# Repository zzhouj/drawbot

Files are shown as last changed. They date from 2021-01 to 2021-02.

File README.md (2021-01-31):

# drawbot
2040铝合金框架Core-XY结构的写字机器人

## 简介
打印机墨盒又双叕涨价了！娃经常要我帮她抄写错题，费时费力，还嫌弃我字写的难看。不如自己DIY一台写字机器人，既可以替代我抄写错题，还可以部分替代打印机的功能节省墨（Jin）盒（Qian）。

本项目主要参考了[T站](https://www.thingiverse.com/)上的[DrawBot V1.1 (Drawing Robot - Arduino Uno + CNC Shield + GRBL)](https://www.thingiverse.com/thing:2349232)。参考项目的机械部分采用了3D打印件，而我手头暂时还没有3D打印机，所以采用了2040铝合金的框架以及某宝上定制CNC切割了5块3mm铝合金板，电子部分和软件部分和参考项目一样。

做这个项目主要是考虑到DIY写字机器人相对DIY 3D打印机来说要简单很多：没有Z轴，没有热床，没有挤出机，一块Arduino Uno + CNC Shield即可控制，GRBL firmware复杂度低。我想先用写字机器人来练手，然后再来自己组装一台3D打印机。

## 目录及文件说明
- sw2020/ 存放写字机器人的零件模型及装配文件，使用的三维建模软件是SolidWorks 2020。
- dxf/ 3mm铝合金板定制CNC切割文件，由sw2020文件夹中的对应零件模型导出生成。
- bom/ 各部分材料清单。
- BOM.xls 零件清单及参考价格。
- Assemble and User Manual.pdf 装配及用户手册。

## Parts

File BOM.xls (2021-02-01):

项目号 | 零件号 | 说明 | 数量 | 单价 | 价格
1 | V-Slot 2040铝型材370mm | 欧标V-Slot | 1 | 9.22 | 9.22
2 | V-Slot 2040铝型材200mm | 欧标V-Slot | 2 | 4.98 | 9.96
3 | 7878_2020角铝20x8mm |  | 4 | 3.5 | 14
4 | T型螺母20M6 |  | 16 | 0.2 | 3.2
5 | B18.3.4M - 6 x 1.0 x 12 SBHCS --N | 圆头内六角M6*12 | 16 | 0.15 | 2.4
6 | 2040铝合金型材盖板 |  | 8 | 2.5 | 20
7 | B18.3.5M - 5 x 0.8 x 10 Socket FCHS -- 10N | 沉头内六角M5*10 | 16 | 0.21 | 3.36
8 | T型螺母20M5 |  | 16 | 0.2 | 3.2
9 | 42步进电机支架 |  | 2 | 2.9 | 5.8
10 | B18.3.4M - 4 x 0.7 x 8 SBHCS --N | 圆头内六角M4*8 | 8 | 0.06 | 0.48
11 | T型螺母20M4 |  | 8 | 0.2 | 1.6
12 | 光轴固定支架（卧式）SHF8 |  | 8 | 2.6 | 20.8
13 | 光轴8x370mm |  | 4 | 5.8 | 23.2
14 | B18.3.4M - 5 x 0.8 x 16 SBHCS --N | 圆头内六角M5*16 | 16 | 0.12 | 1.92
15 | XY轴联合支架 | 3mm铝合金板定制CNC切割 | 1 | 18 | 18
16 | 光轴轴承LM8UU |  | 8 | 2 | 16
17 | B18.3.4M - 5 x 0.8 x 25 SBHCS --N | 圆头内六角M5*25 | 4 | 0.16 | 0.64
18 | 2GT惰轮20齿无齿内孔5 带宽6mm |  | 5 | 3.1 | 15.5
19 | B18.2.4.1M - Hex nut, Style 1, M5 x 0.8 --D-N | 螺母M5 | 4 | 0.06 | 0.24
20 | B18.2.4.5M - Hex jam nut, M5 x 0.8 --D-N | 螺母M5 | 8 | 0.06 | 0.48
21 | Y轴尾端 |  | 1 | 18 | 18
22 | 圆柱销M5x25mm |  | 1 | 0.5 | 0.5
23 | Y轴首端 |  | 1 | 18 | 18
24 | 六角隔离柱M3x6mm |  | 4 | 1.56 | 6.24
25 | Y轴首端——销柱支架 |  | 1 | 18 | 18
26 | B18.3.4M - 3 x 0.5 x 6 SBHCS --N | 圆头内六角M3*6 | 6 | 0.06 | 0.36
27 | 舵机SG90 |  | 1 | 4.9 | 4.9
28 | ABS空心隔离柱5.2x11x1 2mm |  | 4 | 0.23 | 0.92
29 | 圆柱销M6x120mm |  | 2 | 0.95 | 1.9
30 | B18.2.4.5M - Hex jam nut, M5 x 0.8 --D-N | 螺母M5 | 4 | 0.06 | 0.24
31 | B18.2.4.1M - Hex nut, Style 1, M3 x 0.5 --D-N | 螺母M3 | 4 | 0.05 | 0.2
32 | Y轴首端——滑动支架 |  | 1 | 18 | 18
33 | 夹笔器 |  | 1 | 20 | 20
34 | 光轴轴承LM6UU |  | 4 | 1.4 | 5.6
35 | 42步进电机38mm | 二手拆机件 | 2 | 12.68 | 25.36
36 | 2GT同步轮20齿内孔5带 宽6mm |  | 2 | 1.7 | 3.4
37 | B18.3.1M - 3 x 0.5 x 8 Hex SHCS -- 8NHX | 杯头内六角M3*8 | 8 | 0.1 | 0.8
38 | 42步进电机硅胶减震垫片 厚2mm |  | 2 | 1.76 | 3.52
39 | Arduino Uno |  | 1 | 19.5 | 19.5
40 | CNC Shield V3 + A4988x4 |  | 1 | 19.4 | 19.4
41 | 42步进电机连接线 |  | 2 | 1.5 | 3
42 | 2GT同步带6mm |  | 2 | 2.65 | 5.3
43 | 2pin杜邦线（公对母）70cm |  | 2 | 0.8 | 1.6
44 | 六角隔离柱M3x20mm |  | 4 | 1.68 | 6.72
45 | 跳线帽 |  | 6 | 0.04 | 0.24
46 | 电源适配器12V2A |  | 1 | 12.8 | 12.8
47 | 2芯1平方保护套软电线0.2m |  | 1 | 0.26 | 0.26
48 | 电源接头DC母头 |  | 1 | 0.6 | 0.6
合计 |  |  | 225 |  | 385.36

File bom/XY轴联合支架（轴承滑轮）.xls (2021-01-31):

项目号 | 零件号 | 说明 | 数量
1 | XY轴联合支架 |  | 1
2 | 光轴轴承LM8UU |  | 8
3 | B18.3.4M - 5 x 0.8 x 25 SBHCS --N |  | 4
4 | 2GT惰轮20齿无齿内孔5 带宽6mm |  | 4
5 | B18.2.4.1M - Hex nut, Style 1, M5 x 0.8 --D-N |  | 4
6 | B18.2.4.5M - Hex jam nut, M5 x 0.8 --D-N |  | 4

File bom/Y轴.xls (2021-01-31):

项目号 | 零件号 | 说明 | 数量
1 | Y轴尾端 |  | 1
2 | 圆柱销M5x25mm |  | 1
3 | 2GT惰轮20齿无齿内孔5 带宽6mm |  | 1
4 | 光轴固定支架（卧式）SH F8 |  | 4
5 | B18.3.4M - 5 x 0.8 x 16 SBHCS --N |  | 8
6 | B18.2.4.5M - Hex jam nut, M5 x 0.8 --D-N |  | 4
7 | 光轴8x370mm |  | 2
8 | Y轴首端 |  | 1
9 | 六角隔离柱M3x6mm |  | 4
10 | Y轴首端——销柱支架 |  | 1
11 | B18.3.4M - 3 x 0.5 x 6 SBHCS --N |  | 4
12 | 舵机SG90 |  | 1
13 | ABS空心隔离柱5.2x11x1 2mm |  | 4
14 | 圆柱销M6x120mm |  | 2
15 | B18.2.4.5M - Hex jam nut, M5 x 0.8 --D-N |  | 4
16 | B18.2.4.1M - Hex nut, Style 1, M3 x 0.5 --D-N |  | 4

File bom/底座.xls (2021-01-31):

项目号 | 零件号 | 说明 | 数量
1 | V-Slot 2040铝型材370mm |  | 1
2 | V-Slot 2040铝型材200mm |  | 2
3 | 7878_2020角铝20x8m m |  | 4
4 | T型螺母20M6 |  | 16
5 | B18.3.4M - 6 x 1.0 x 12 SBHCS --N | 圆头内六角M6*12 | 16
6 | 2040铝合金型材盖板 |  | 8
7 | B18.3.5M - 5 x 0.8 x 10 Socket FCHS -- 10N |  | 16
8 | T型螺母20M5 |  | 8
9 | 42步进电机支架 |  | 2
10 | B18.3.4M - 4 x 0.7 x 8 SBHCS --N |  | 8
11 | T型螺母20M4 |  | 8

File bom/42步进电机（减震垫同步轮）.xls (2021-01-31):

项目号 | 零件号 | 说明 | 数量
1 | 42步进电机38mm |  | 1
2 | 2GT同步轮20齿内孔5带 宽6mm |  | 1
3 | B18.3.1M - 3 x 0.5 x 8 Hex SHCS -- 8NHX |  | 4
4 | 42步进电机硅胶减震垫 片厚2mm |  | 1

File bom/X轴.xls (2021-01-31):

项目号 | 零件号 | 说明 | 数量
1 | 光轴固定支架（卧式）S HF8 |  | 4
2 | 光轴8x370mm |  | 2
3 | B18.3.4M - 5 x 0.8 x 16 SBHCS --N |  | 8
4 | T型螺母20M5 |  | 8

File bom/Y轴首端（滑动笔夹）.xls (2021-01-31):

项目号 | 零件号 | 说明 | 数量
1 | Y轴首端——滑动支架 |  | 1
2 | 夹笔器 |  | 1
3 | B18.3.4M - 3 x 0.5 x 6 SBHCS --N |  | 2
4 | 光轴轴承LM6UU |  | 4

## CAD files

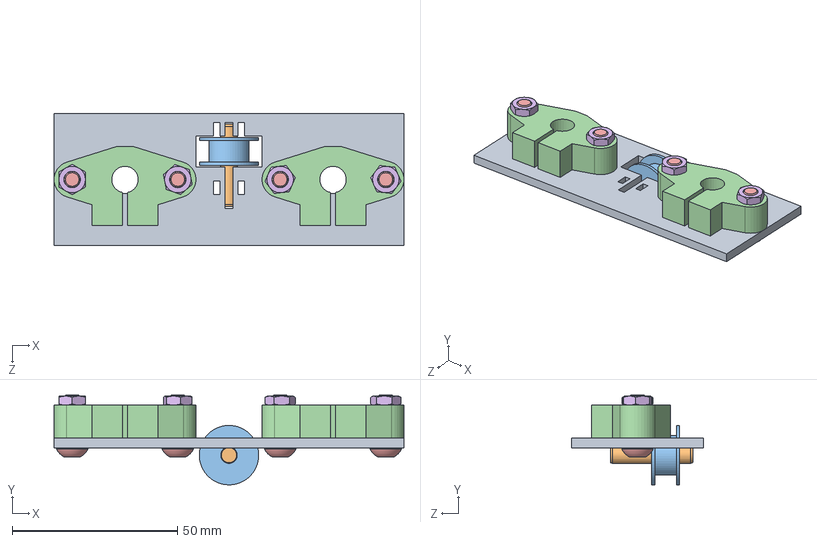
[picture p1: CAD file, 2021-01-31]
sw2020/写字机器人——Y轴尾端.SLDASM
106.0 x 27.2 x 40.0 mm
Y轴尾端
圆柱销M5x25mm
2GT惰轮20齿无齿内孔5带宽6mm
光轴固定支架（卧式）SHF8 x 2
socket button head cap screw_am x 4
hex nut jam_am x 4

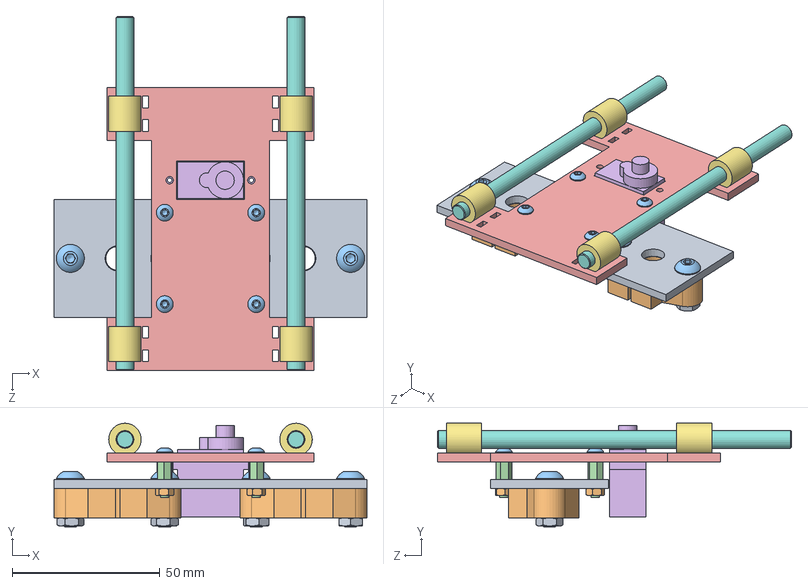
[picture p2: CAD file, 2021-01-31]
sw2020/写字机器人——Y轴首端（固定支架）.SLDASM
106.0 x 35.1 x 120.0 mm
Y轴首端
光轴固定支架（卧式）SHF8 x 2
socket button head cap screw_am x 8
六角隔离柱M3x6mm x 4
Y轴首端——销柱支架
舵机SG90
ABS空心隔离柱5.2x11x12mm x 4
圆柱销M6x120mm x 2
B18.2.4.5M - Hex jam nut, M5 x 0.8 --D-N x 4
hex nut style 1_am x 4

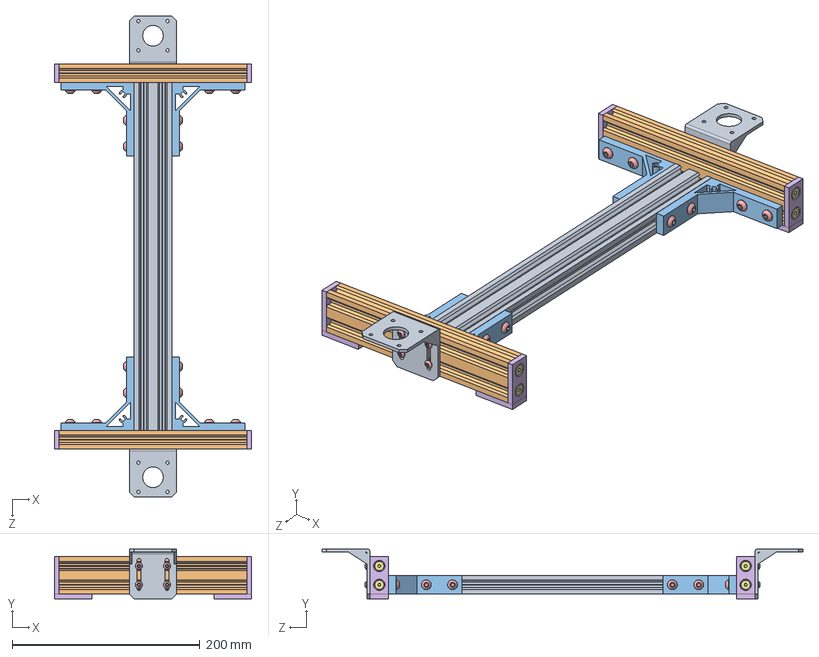
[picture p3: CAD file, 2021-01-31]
sw2020/写字机器人——底座.SLDASM
210.0 x 53.0 x 512.0 mm
V-Slot 2040铝型材370mm
V-Slot 2040铝型材200mm x 2
7878_2020角铝20x8mm x 4
T型螺母20M6 x 16
socket button head cap screw_am x 24
2040铝合金型材盖板 x 8
socket countersunk head screw_am x 16
T型螺母20M5 x 8
42步进电机支架 x 2
T型螺母20M4 x 8

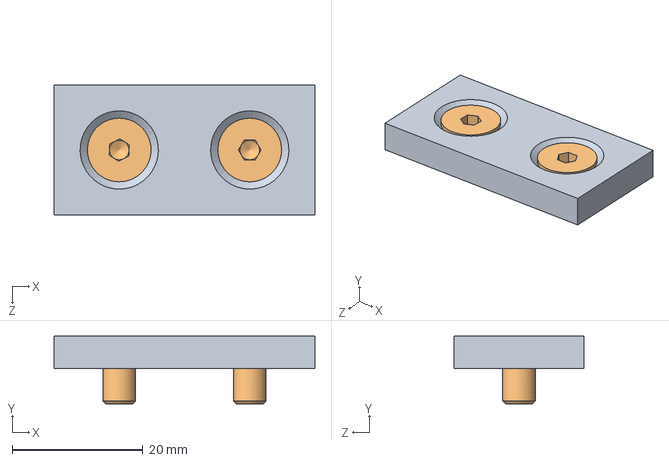
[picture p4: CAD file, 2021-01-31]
sw2020/2040铝合金型材盖板（已紧固）.SLDASM
40.0 x 10.4 x 20.0 mm
2040铝合金型材盖板
socket countersunk head screw_am x 2

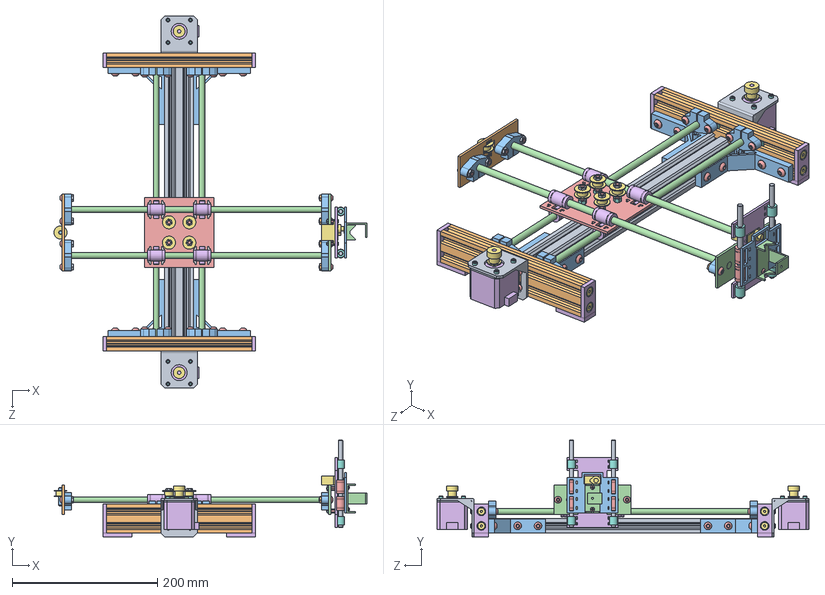
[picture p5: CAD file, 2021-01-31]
sw2020/写字机器人（总装）.SLDASM
431.0 x 133.0 x 512.0 mm
V-Slot 2040铝型材370mm
V-Slot 2040铝型材200mm x 2
7878_2020角铝20x8mm x 4
T型螺母20M6 x 16
socket button head cap screw_am x 50
2040铝合金型材盖板 x 8
socket countersunk head screw_am x 16
T型螺母20M5 x 16
42步进电机支架 x 2
T型螺母20M4 x 8
光轴固定支架（卧式）SHF8 x 8
光轴8x370mm x 4
XY轴联合支架
光轴轴承LM8UU x 8
2GT惰轮20齿无齿内孔5带宽6mm x 5
hex nut style 1_am x 8
hex nut jam_am x 8
Y轴尾端
圆柱销M5x25mm
Y轴首端
六角隔离柱M3x6mm x 4
Y轴首端——销柱支架
舵机SG90
ABS空心隔离柱5.2x11x12mm x 4
圆柱销M6x120mm x 2
B18.2.4.5M - Hex jam nut, M5 x 0.8 --D-N x 4
Y轴首端——滑动支架
夹笔器
光轴轴承LM6UU x 4
42步进电机38mm x 2
2GT同步轮20齿内孔5带宽6mm x 2
socket head cap screw_am x 8
42步进电机硅胶减震垫片厚2mm x 2

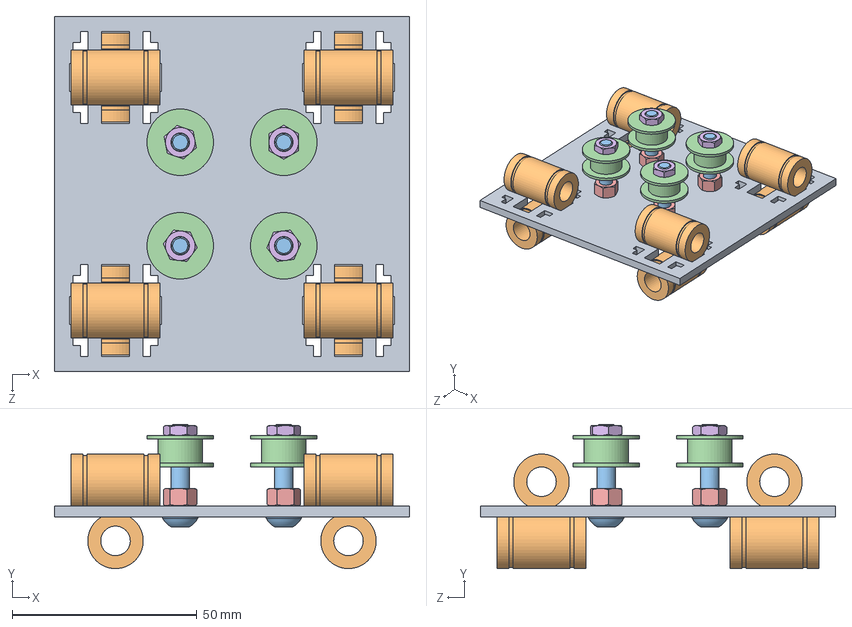
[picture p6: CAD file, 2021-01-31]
sw2020/写字机器人——XY轴联合支架（轴承滑轮）.SLDASM
96.0 x 39.0 x 96.0 mm
XY轴联合支架
光轴轴承LM8UU x 8
socket button head cap screw_am x 4
2GT惰轮20齿无齿内孔5带宽6mm x 4
hex nut style 1_am x 4
hex nut jam_am x 4

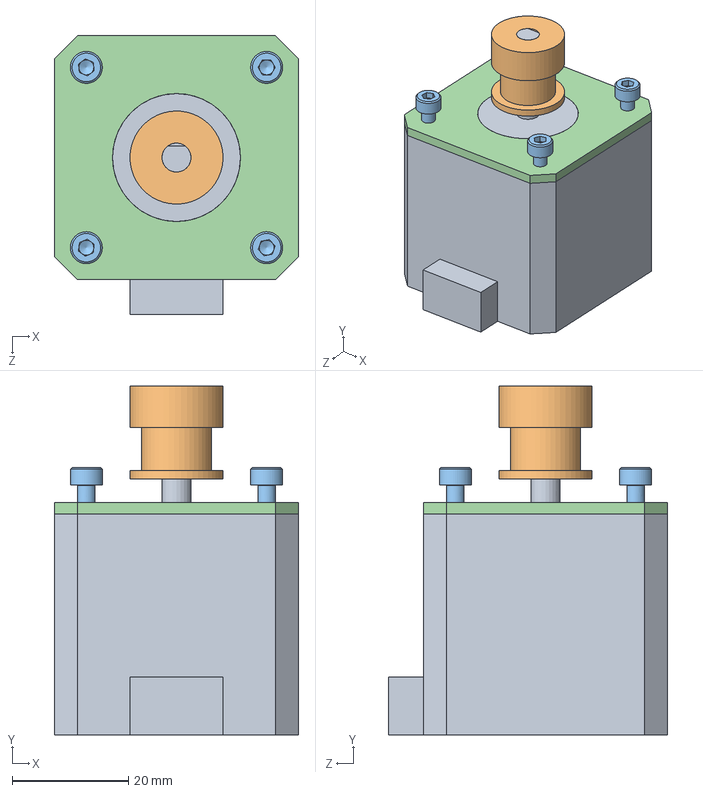
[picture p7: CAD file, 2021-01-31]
sw2020/42步进电机（减震垫同步轮）.SLDASM
42.0 x 60.0 x 48.0 mm
42步进电机38mm
2GT同步轮20齿内孔5带宽6mm
socket head cap screw_am x 4
42步进电机硅胶减震垫片厚2mm

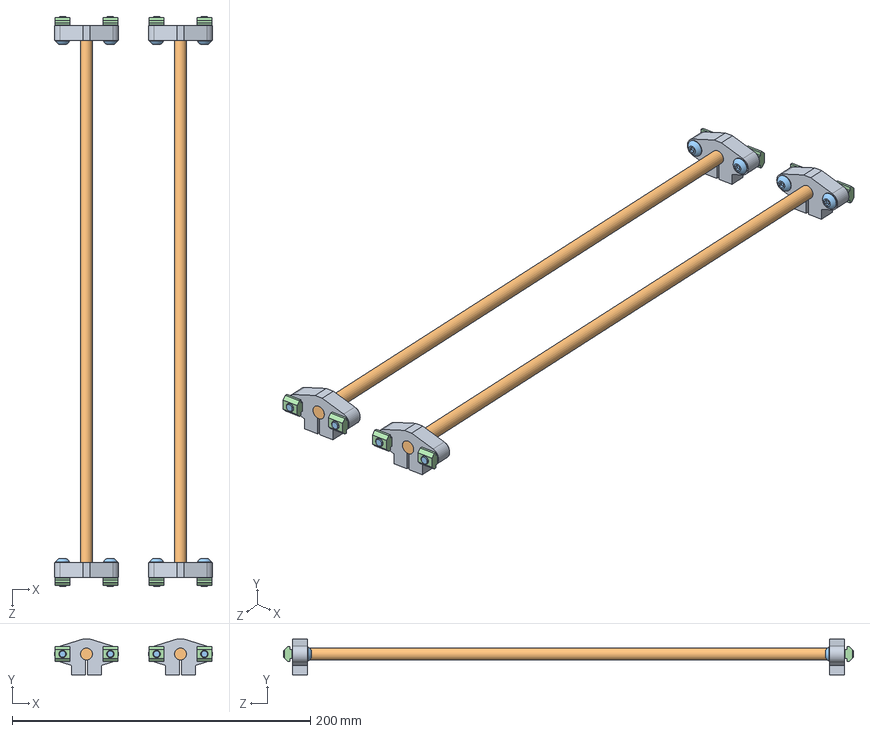
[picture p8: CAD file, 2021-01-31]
sw2020/写字机器人——X轴.SLDASM
106.0 x 24.0 x 382.0 mm
光轴固定支架（卧式）SHF8 x 4
光轴8x370mm x 2
socket button head cap screw_am x 8
T型螺母20M5 x 8

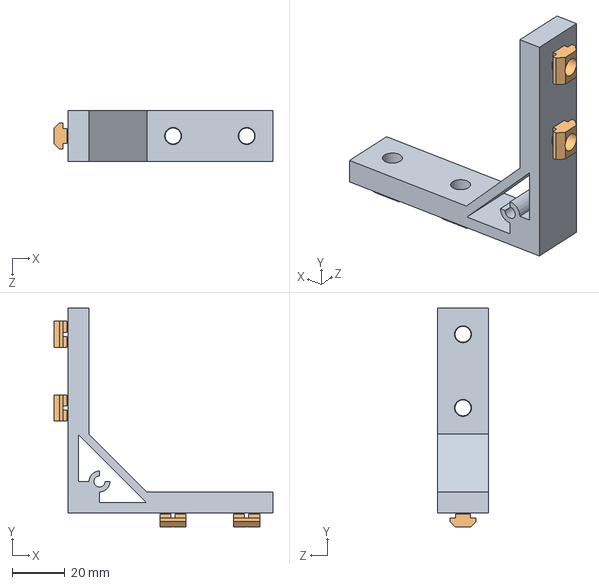
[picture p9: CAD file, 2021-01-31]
sw2020/7878_2020角铝20x8mm（已紧固）.SLDASM
83.3 x 83.3 x 19.5 mm
7878_2020角铝20x8mm
T型螺母20M6 x 4

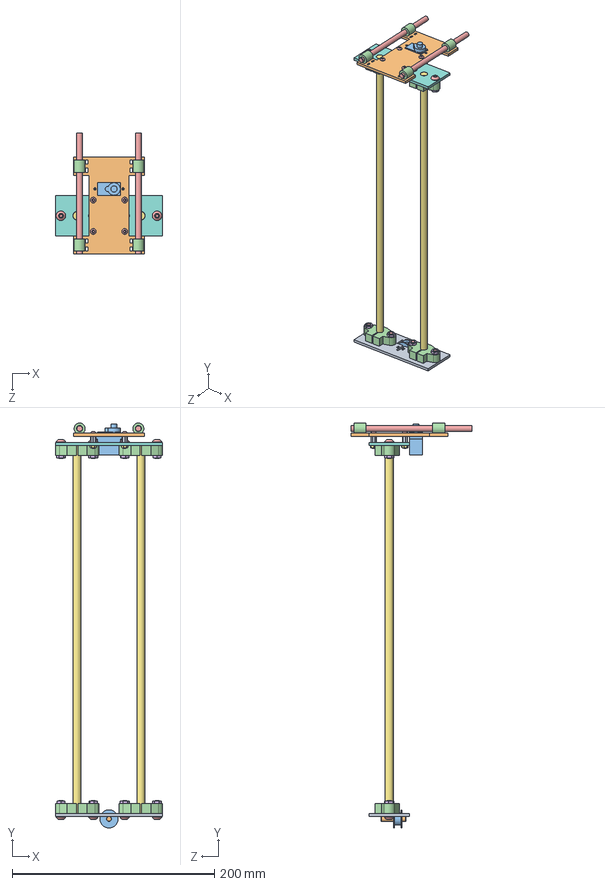
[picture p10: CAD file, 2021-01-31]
sw2020/写字机器人——Y轴.SLDASM
106.0 x 400.3 x 120.0 mm
Y轴尾端
圆柱销M5x25mm
2GT惰轮20齿无齿内孔5带宽6mm
光轴固定支架（卧式）SHF8 x 4
socket button head cap screw_am x 12
hex nut jam_am x 4
光轴8x370mm x 2
Y轴首端
六角隔离柱M3x6mm x 4
Y轴首端——销柱支架
舵机SG90
ABS空心隔离柱5.2x11x12mm x 4
圆柱销M6x120mm x 2
B18.2.4.5M - Hex jam nut, M5 x 0.8 --D-N x 4
hex nut style 1_am x 4

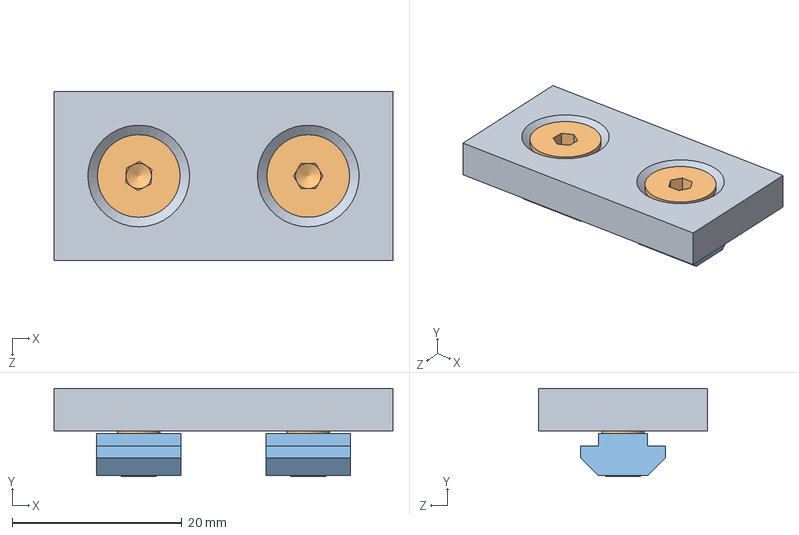
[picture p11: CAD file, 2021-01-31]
sw2020/2040铝合金型材盖板（已紧固——T型螺母）.SLDASM
40.0 x 10.4 x 20.0 mm
2040铝合金型材盖板
socket countersunk head screw_am x 2
T型螺母20M5 x 2

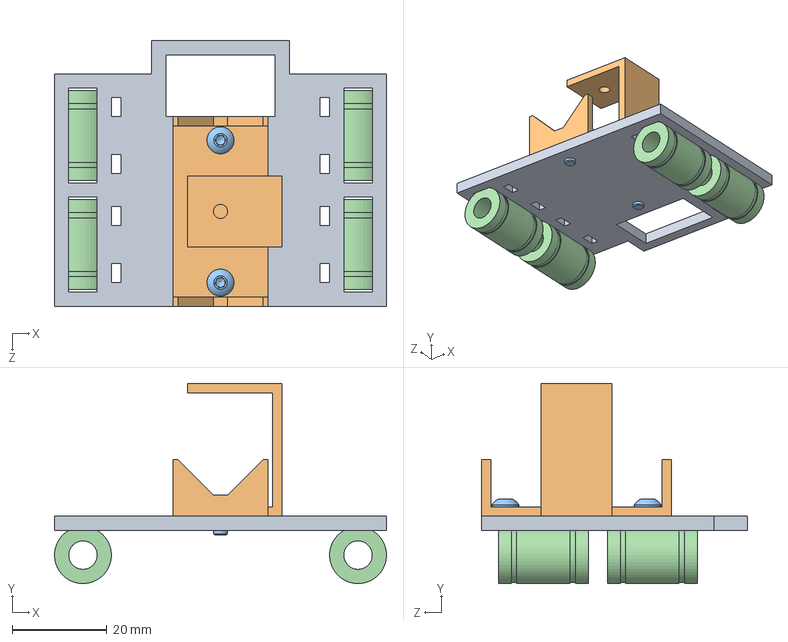
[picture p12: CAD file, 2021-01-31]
sw2020/写字机器人——Y轴首端（滑动笔夹）.SLDASM
70.0 x 42.2 x 56.0 mm
Y轴首端——滑动支架
夹笔器
socket button head cap screw_am x 2
光轴轴承LM6UU x 4

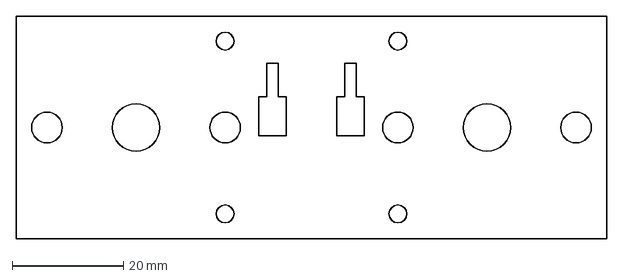
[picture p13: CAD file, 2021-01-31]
dxf/Y轴首端.DXF
106.0 x 40.0 mm

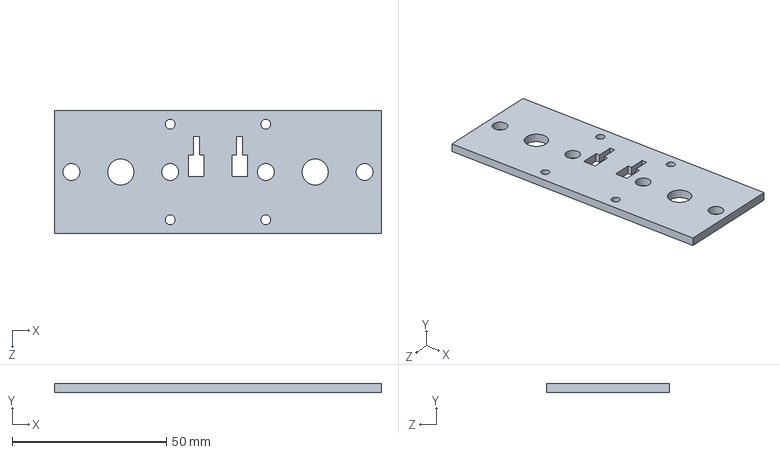
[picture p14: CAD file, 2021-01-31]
sw2020/Y轴首端.SLDPRT
106.0 x 3.00 x 40.0 mm

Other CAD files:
dxf/Y轴尾端.DXF
sw2020/圆柱销M6x120mm.SLDPRT
dxf/Y轴首端——销柱支架.DXF
sw2020/2GT同步轮20齿内孔5带宽6mm.SLDPRT
dxf/XY轴联合支架.DXF
dxf/Y轴首端——滑动支架.DXF
sw2020/2040铝合金型材盖板.SLDPRT
sw2020/2GT惰轮20齿无齿内孔5带宽6mm.SLDPRT
sw2020/42步进电机38mm.SLDPRT
sw2020/42步进电机支架.SLDPRT
sw2020/42步进电机硅胶减震垫片厚2mm.SLDPRT
sw2020/7878_2020角铝20x8mm.SLDPRT
sw2020/ABS空心隔离柱5.2x11x12mm.SLDPRT
sw2020/T型螺母20M4.SLDPRT
sw2020/T型螺母20M5.SLDPRT
sw2020/T型螺母20M6.SLDPRT
sw2020/V-Slot 2040铝型材200mm.SLDPRT
sw2020/V-Slot 2040铝型材370mm.SLDPRT
sw2020/XY轴联合支架.SLDPRT
sw2020/Y轴尾端.SLDPRT
sw2020/Y轴首端——滑动支架.SLDPRT
sw2020/Y轴首端——销柱支架.SLDPRT
sw2020/光轴8x370mm.SLDPRT
sw2020/光轴固定支架（卧式）SHF8.SLDPRT
sw2020/光轴轴承LM6UU.SLDPRT
sw2020/光轴轴承LM8UU.SLDPRT
sw2020/六角隔离柱M3x6mm.SLDPRT
sw2020/圆柱销M5x25mm.SLDPRT
sw2020/夹笔器.SLDPRT
sw2020/舵机SG90.SLDPRT

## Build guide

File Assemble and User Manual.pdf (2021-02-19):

# 装配及用户手册

目录

## 0 简介

打印机墨盒又双叕涨价了！娃经常要我帮她抄写错题，费时费力，还嫌弃我字写的难看。不 如自己 DIY 一台写字机器人，既可以替代我抄写错题，还可以部分替代打印机的功能节省墨
（Jin）盒（Qian）。

本项目主要参考了 T 站上的 (https://www.thingiverse.com/) DrawBot V1.1 (https://www.thingiverse.com/thing:2349232) (Drawing Robot - Arduino Uno + CNC Shield + GRBL)。
参考项目的机械部分采用了 3D 打印件，而我手头暂时还没有 3D 打印机，所以采用了 2040 铝合金的框架以及某宝上定制 CNC 切割了 5 块 3mm 铝合金板，电子部分和软件部分和参考 项目一样。

本项目为开源项目，项目主页：https://github.com/zzhouj/drawbot。目录及文件说明：
- sw2020/ 存放写字机器人的零件模型及装配文件，使用的三维建模软件是 SolidWorks
2020。
- dxf/ 3mm 铝合金板定制 CNC 切割文件，由 sw2020 文件夹中的对应零件模型导出生成。
- bom/ 各部分材料清单。
- BOM.xls 零件清单及参考价格。
- Assemble and User Manual.pdf 装配及用户手册。 1 机械部分

### 1.0 准备工作

切口打磨

2040 铝合金型材和 7878 角铝的切口，以及 3mm 铝合金板激光切口背面会有毛刺，在装配 过程中容易划伤手。所以在进行装配前，需要对有毛刺的切口进行打磨和抛光。可以使用打 磨块或者打磨板+带背胶的砂纸，按照粗磨（240 目），细磨（1000 目），抛光（4000 目） 的顺序进行打磨。注意：打磨时戴上口罩和手套进行防护。

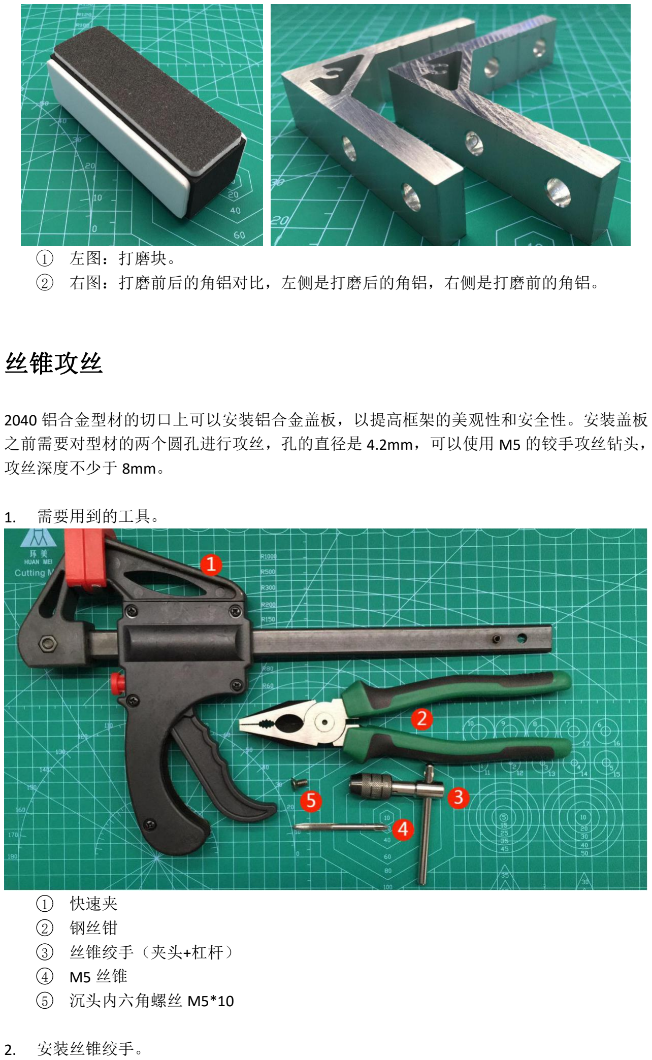
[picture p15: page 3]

1 | 左图：打磨块。
2 | 右图：打磨前后的角铝对比，左侧是打磨后的角铝，右侧是打磨前的角铝。 丝锥攻丝

2040 铝合金型材的切口上可以安装铝合金盖板，以提高框架的美观性和安全性。安装盖板 之前需要对型材的两个圆孔进行攻丝，孔的直径是 4.2mm，可以使用 M5 的铰手攻丝钻头， 攻丝深度不少于 8mm。

1. 需要用到的工具。
1 | 快速夹
2 | 钢丝钳
3 | 丝锥绞手（夹头+杠杆）
4 | M5 丝锥
5 | 沉头内六角螺丝 M5*10
2. 安装丝锥绞手。

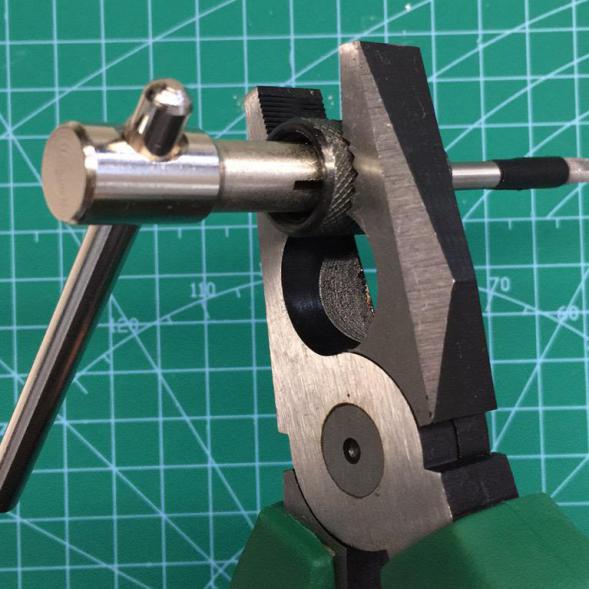
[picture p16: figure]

1 左图：根据参考螺丝，使用电工胶布标记攻丝深度，注意丝锥头部大约 5mm 不是 有效区域。
2 右图：使用钢丝钳夹住丝锥夹头，转动绞手杠杆拧紧丝锥夹头。
3. 攻丝。

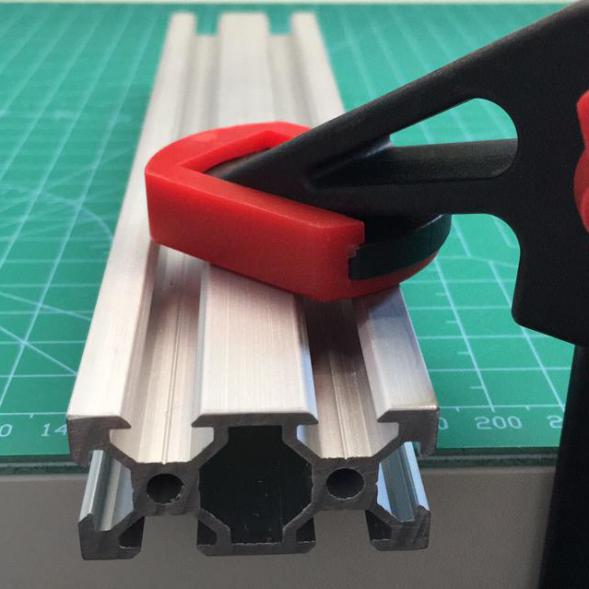
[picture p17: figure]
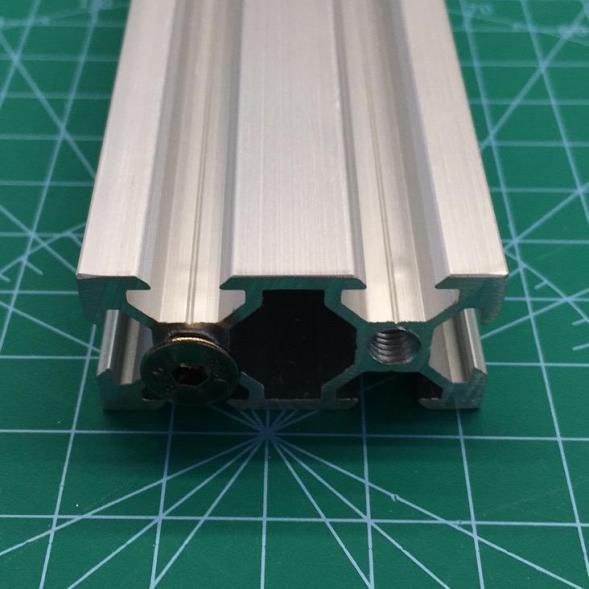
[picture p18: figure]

1 | 左图：使用快速夹将 2040 铝型材固定在桌面边缘。
2 | 右图：完成后使用参考螺丝测试丝路是否顺滑。
3 | 攻丝的过程中需要不断的重复攻丝，退丝，清理（金属碎屑）的循环，直至达到预
定深度，并在达到预定深度后在执行几次循环，将丝路清理干净。
4 攻丝过程中，孔口由于受到挤压，会产生突起的毛刺，攻丝完成后可用凿刀将孔口 清理干净。

## 1.1 底座及 X 轴

底座

1. 材料及工具。
1 | V-Slot 2040 铝型材 370mm
2 | V-Slot 2040 铝型材 200mm x2
3 | 7878_2020 角铝 20x8mm x4
4 | 2040 铝合金型材盖板 x9
5 | T 型螺母 20M6 x16
6 | T 型螺母 20M5 x16
7 | T 型螺母 20M4 x8
8 | 圆头内六角 M6*14 x16
9 | 沉头内六角 M5*10 x18
10 | 圆头内六角 M4*8 x8
11 | M2.5/M3/M4 六角扳手
12 | 42 步进电机支架 x2（拍照时遗漏了...）
2. 2040 铝合金盖板安装（2040 铝型材 370mm 单侧）。

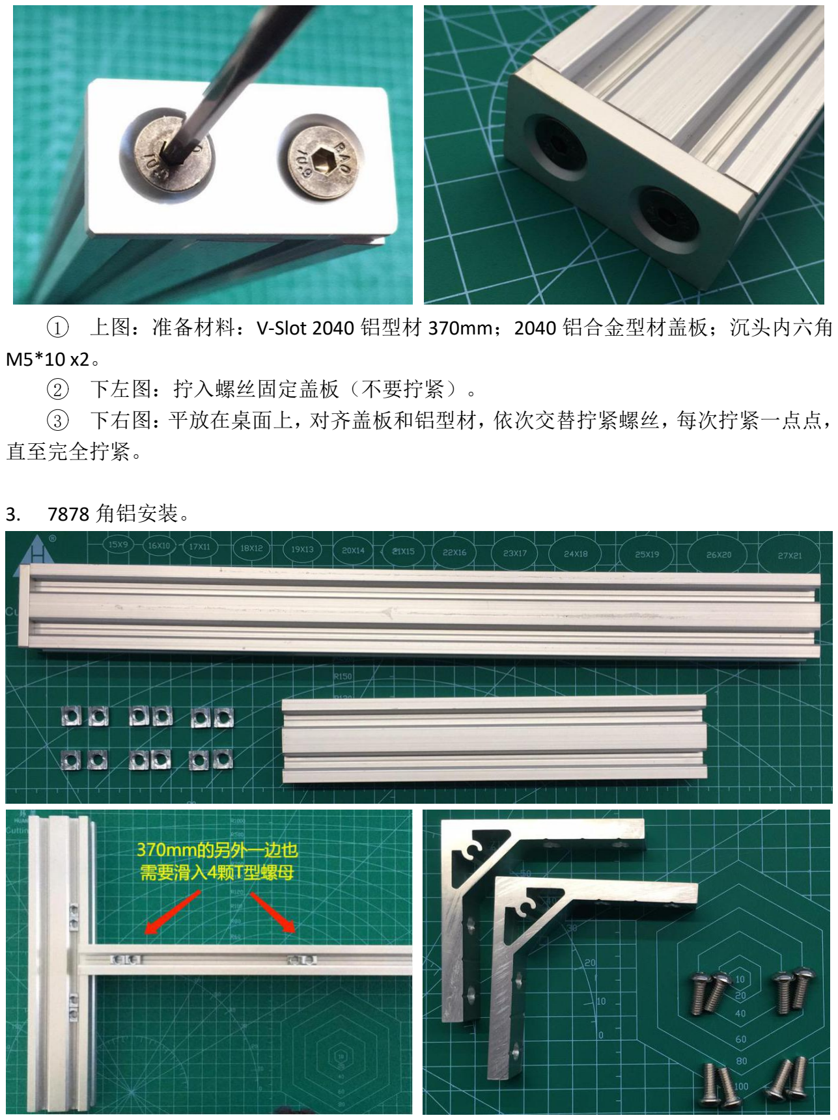
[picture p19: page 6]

1 上图：准备材料：V-Slot 2040 铝型材 370mm；2040 铝合金型材盖板；沉头内六角
M5*10 x2。
2 | 下左图：拧入螺丝固定盖板（不要拧紧）。
3 | 下右图：平放在桌面上，对齐盖板和铝型材，依次交替拧紧螺丝，每次拧紧一点点，
直至完全拧紧。
3. 7878 角铝安装。

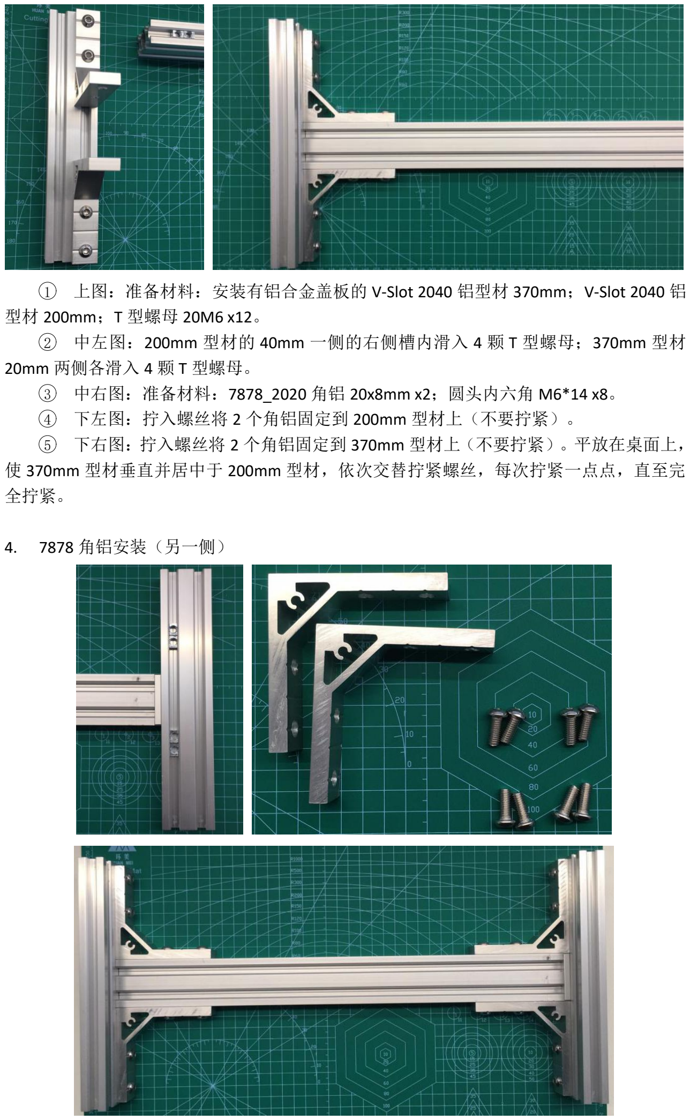
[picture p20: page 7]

1 上图：准备材料：安装有铝合金盖板的 V-Slot 2040 铝型材 370mm；V-Slot 2040 铝 型材 200mm；T 型螺母 20M6 x12。
2 中左图：200mm 型材的 40mm 一侧的右侧槽内滑入 4 颗 T 型螺母；370mm 型材 20mm 两侧各滑入 4 颗 T 型螺母。
3 | 中右图：准备材料：7878_2020 角铝 20x8mm x2；圆头内六角 M6*14 x8。
4 | 下左图：拧入螺丝将 2 个角铝固定到 200mm 型材上（不要拧紧）。
5 | 下右图：拧入螺丝将 2 个角铝固定到 370mm 型材上（不要拧紧）。平放在桌面上，
使 370mm 型材垂直并居中于 200mm 型材，依次交替拧紧螺丝，每次拧紧一点点，直至完 全拧紧。
4. 7878 角铝安装（另一侧）

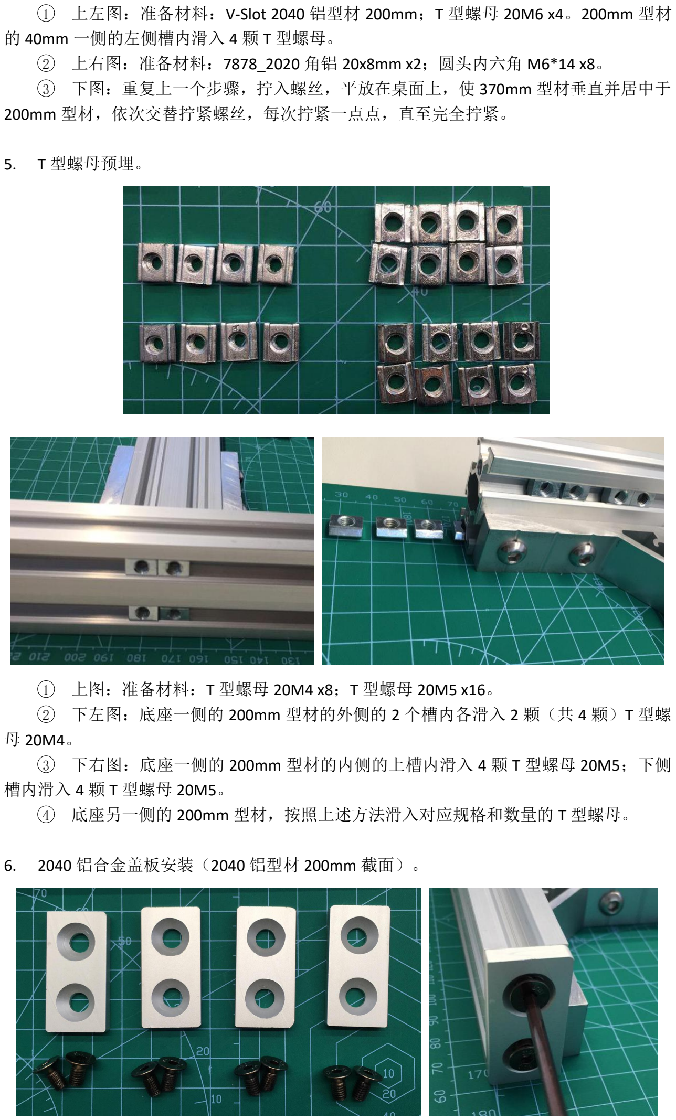
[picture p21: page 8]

1 上左图：准备材料：V-Slot 2040 铝型材 200mm；T 型螺母 20M6 x4。200mm 型材
的 40mm 一侧的左侧槽内滑入 4 颗 T 型螺母。
2 | 上右图：准备材料：7878_2020 角铝 20x8mm x2；圆头内六角 M6*14 x8。
3 | 下图：重复上一个步骤，拧入螺丝，平放在桌面上，使 370mm 型材垂直并居中于
200mm 型材，依次交替拧紧螺丝，每次拧紧一点点，直至完全拧紧。
5. T 型螺母预埋。
1 | 上图：准备材料：T 型螺母 20M4 x8；T 型螺母 20M5 x16。
2 | 下左图：底座一侧的 200mm 型材的外侧的 2 个槽内各滑入 2 颗（共 4 颗）T 型螺
母 20M4。
3 下右图：底座一侧的 200mm 型材的内侧的上槽内滑入 4 颗 T 型螺母 20M5；下侧 槽内滑入 4 颗 T 型螺母 20M5。
4 底座另一侧的 200mm 型材，按照上述方法滑入对应规格和数量的 T 型螺母。
6. 2040 铝合金盖板安装（2040 铝型材 200mm 截面）。

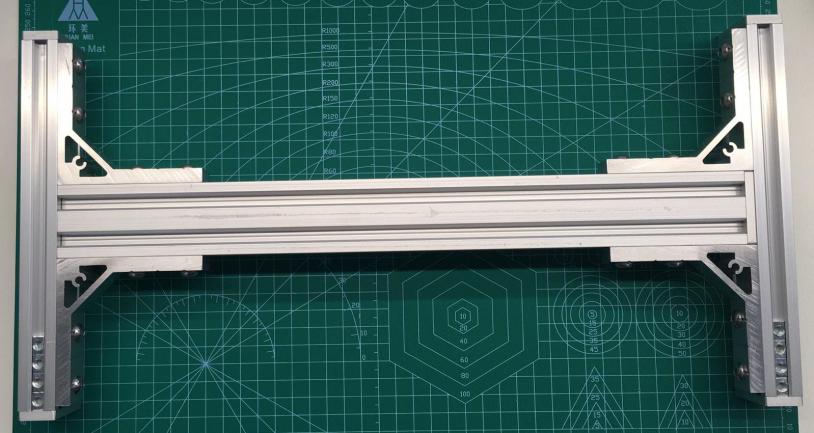
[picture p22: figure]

1 | 上左图：准备材料：2040 铝合金型材盖板 x4；沉头内六角 M5*10 x8。
2 | 上右图：在 200mm 型材的截面处，拧入螺丝固定盖板（不要拧紧），平放在桌面
上，对齐盖板和铝型材，依次交替拧紧螺丝，每次拧紧一点点，直至完全拧紧。
3 下图：按上述步骤，对其余 3 处 200mm 型材的截面安装盖板。图为盖板安装完成 后，整个底座翻转过来（底部朝上），为下一个安装步骤做准备。
7. 2040 铝合金盖板安装（底部）。

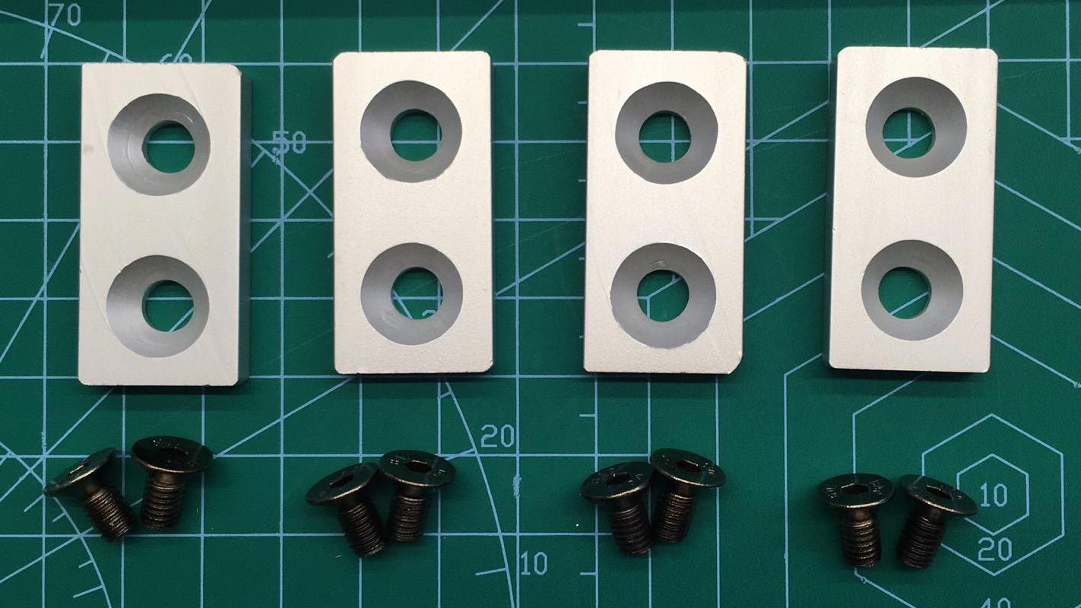
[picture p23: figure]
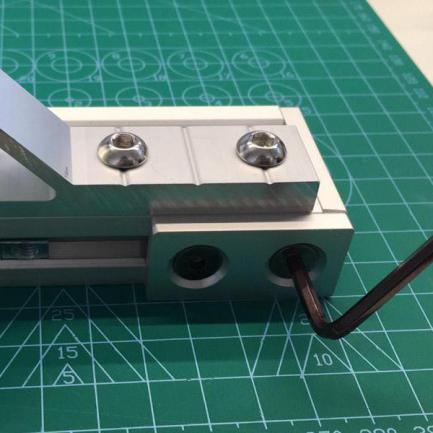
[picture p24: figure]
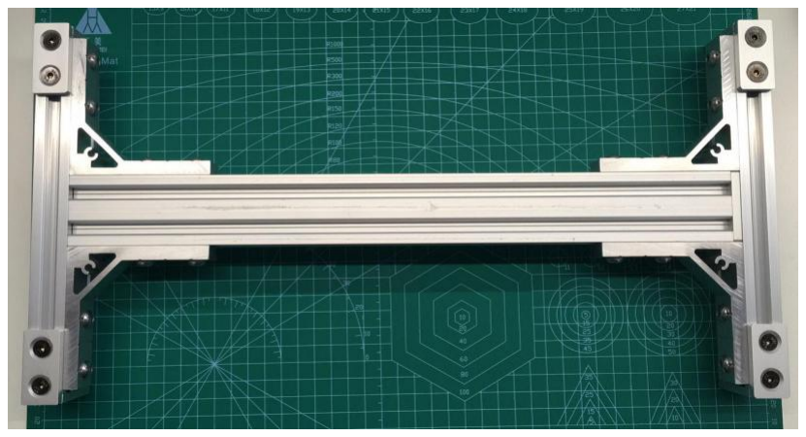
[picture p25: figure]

1 | 上左图：准备材料：2040 铝合金型材盖板 x4；沉头内六角 M5*10 x8。
2 | 上右图：在 200mm 型材的底部边角，拧入螺丝固定盖板（不要拧紧），将整个底
座树立起来，放在桌面上，对齐盖板和铝型材，依次交替拧紧螺丝，每次拧紧一点点，直至 完全拧紧。
3 下图：按上述步骤，对其余 3 处 200mm 型材的底部边角安装盖板。图为底部盖板 安装完成后的状态。

8. 42 步进电机支架安装。

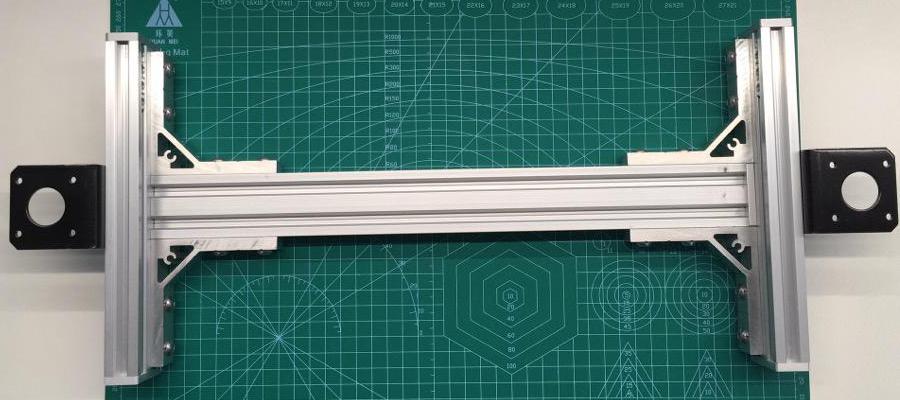
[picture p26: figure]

1 | 上左图：准备材料：42 步进电机支架 x2；圆头内六角 M4*8 x8。
2 | 上右图：拧入螺丝（不要拧紧）将 42 步进电机支架 x2 固定到底座两侧。
3 | 下图：将底座平放在桌面上，使支架底部自然贴住桌面，并将支架居中对齐于
200mm 型材，依次交替拧紧螺丝，每次拧紧一点点，直至完全拧紧。

### 1.2 联合支架及 Y 轴

### 1.3 滑动笔夹

1. 材料及工具。

1 | Y 轴首端——滑动支架
2 | 夹笔器
3 | 光轴轴承 LM6UU x4
4 | 圆头内六角 M3*6 x2
5 | M3 丝锥
6 | 丝锥绞手（夹头+杠杆）
7 | 自锁式尼龙扎带 5*150（宽 3.6mm） x8
2. 安装夹笔器。

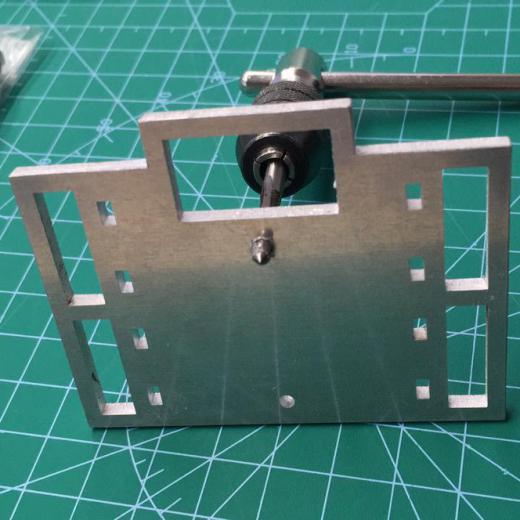
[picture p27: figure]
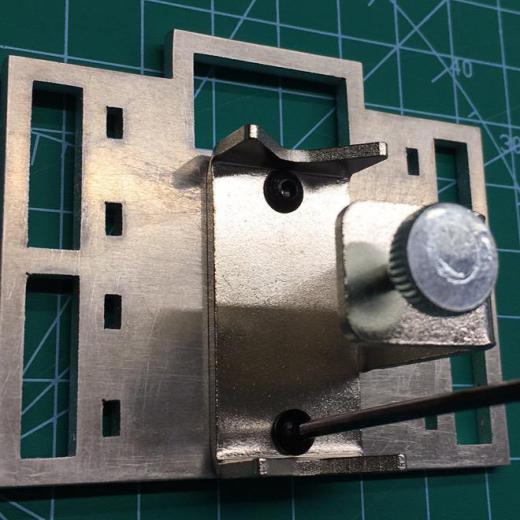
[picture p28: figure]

1 左图：使用 M3 丝锥，对滑动支架上的夹笔器安装孔（两个 2.5mm 的孔）进行攻 丝。
2 右图：拧入螺丝固定夹笔器（不要拧紧）。依次交替拧紧螺丝，每次拧紧一点点， 直至完全拧紧。
3. 安装光轴轴承。

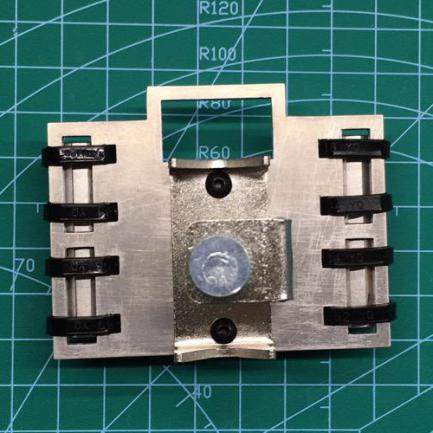
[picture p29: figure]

1 | 上图：准备材料：自锁式尼龙扎带 5*150（宽 3.6mm） x8；光轴轴承 LM6UU x4。
2 | 中左图：将自锁式尼龙扎带从滑动支架背面穿到正面，注意扎带带齿的一面面向外
侧。
3 中右图：在滑动支架背面的槽口内放置好轴承，用扎带扎紧，用剪刀或剪钳剪去扎 带多余部分。
4 | 下左图：安装完毕的滑动笔夹（背面）
5 | 下右图：安装完毕的滑动笔夹（正面）

## 1.4 SG90 舵机

1.5 42 步进电机及同步带

## 2 电子部分

## 2.1 Arduino Uno R3

推荐阅读《Arduino Uno R3 硬件参考》来了解 (http://www.taichi-maker.com/homepage/reference-index/arduino-hardware-refrence/arduino-uno/) Uno R3 的技术参数和引脚说明。

## 2.2 CNC Shield V3 & A4988

推荐阅读《A4988 驱动 NEMA 步进电机(42 步进电机)》或者《 (http://www.taichi-maker.com/homepage/reference-index/motor-reference-index/arduino-a4988-nema-stepper-motor/)A4988 驱动模块使用详解》来 (http://www.lekn.com.cn/newsinfo/2132037.html) 了解 A4988 驱动模块的使用。

推荐阅读《Arduino CNC 电机扩展板详解（A4988 驱动 42 步进电机）》，并测试其中的例子， (http://www.taichi-maker.com/homepage/reference-index/motor-reference-index/arduino-cnc-shield/) 确认 42 步进电机是可以正常工作的，以及接线是正确的。

1. 测试前请先按照《A4988 Vref 电压调节》调节步进电机在工作时流过线圈的电流强度， (http://www.taichi-maker.com/homepage/reference-index/motor-reference-index/arduino-a4988-nema-stepper-motor/)
建议调整到 0.7A 即可。计算公式：I_TripMax= Vref/(8*Rs)。例如：Rs 为 0.1 欧姆，Vref
参考电压就需要调节到 0.56V（0.7A*8*0.1 欧姆）。
2. 测试代码使用了第三方库：AccelStepper 库，请按照《使用 AccelStepper 步进电机库准 (http://www.taichi-maker.com/homepage/reference-index/arduino-library-index/accelstepper-library/)
备工作》中的说明下载和安装好 AccelStepper 库。
3. 编译下载好测试程序，若发现 42 步进电机的主轴不转或者抖动，一般就是两相（两个 线圈）接错，我在测试时就遇到这种情况，后来对照购买的 42 步进电机和 42 步进电机 连接线的说明，才发现原来是两相接错了。
4. 若在测试过程中发现 42 步进电机有失速现象，特别是将测试程序中的 moveSteps 调大 为 2000，并采用全速模式时特别容易出现。此时可以通过降低 setMaxSpeed，或者通过 增加微步细分驱动模式来避免产生电机失速。

## Rs 电阻

通过查看 A4988 驱动模块上面 S1 S2 标号可以确定 Rs 电阻的阻值。

我采购模块的是 0.1 欧姆（标号 R100=0.1 欧姆，R200=0.2 欧姆， R050=0.05 欧姆）。

### 42 步进电机连接线调整

1. 我购买的 42 步进电机和 A4988 驱动模块的引脚说明：

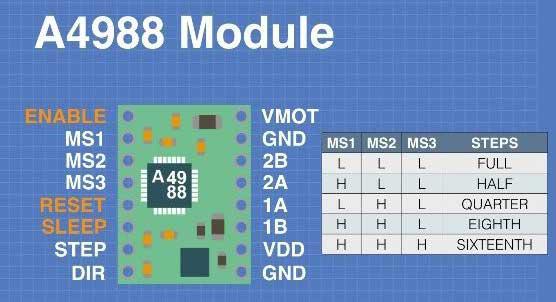
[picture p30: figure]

1 | 左图：电机侧 A+/A-为线圈 1，B+/B-为线圈 2。
2 | 右图：A4988 驱动模块侧 1A/1B 为线圈 1，2A/2B 为线圈 2。
3 | 所以只要 42 步进电机连接线两头的接线顺序一致就不会接错。
2. 购买的 42 步进电机连接线两头的接线顺序：

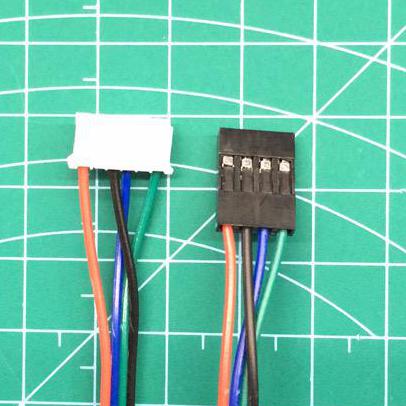
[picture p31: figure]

1 左图：连接线默认状态。XH2.54 侧：红黑为一组，蓝绿为一组；杜邦 2.54 侧：红 蓝为一组，绿黑为一组。处于两相接错状态。
2 右图：连接线调整之后。XH2.54 侧：红黑为一组，蓝绿为一组；杜邦 2.54 侧：红 黑为一组，蓝绿为一组。连接正确。
3. 如何调整杜邦端口接线顺序：

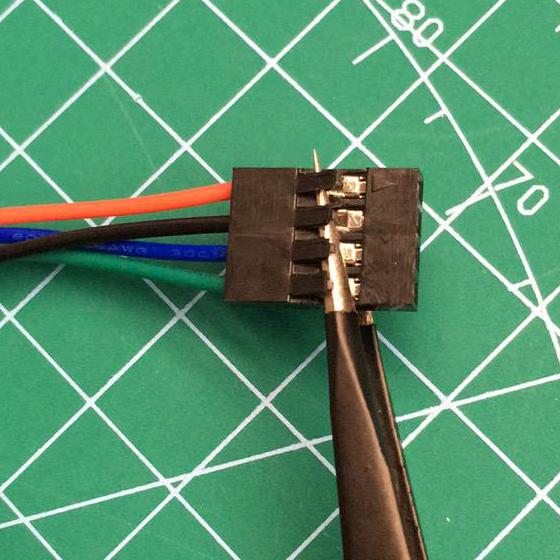
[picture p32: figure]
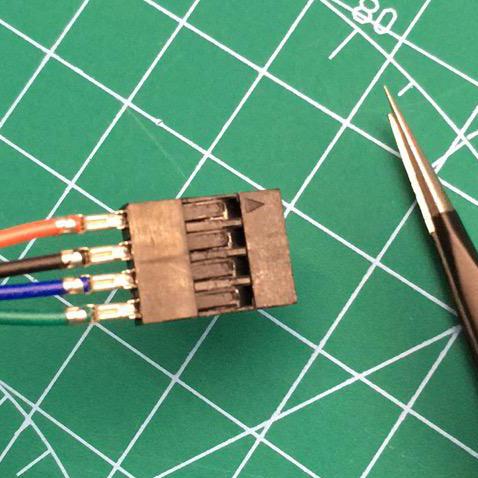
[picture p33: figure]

1 | 左图：先用尖头镊子将杜邦塑料头上的卡子挑起来。
2 | 右图：然后就可以轻松将杜邦线头抽出杜邦外壳。
3 | 调整接线顺序后再插回杜邦外壳，用手按几下原来被挑起的卡子，使其卡住杜邦线
头即可。

## CNC Shield V3 电源接口制作

1. 需要用到的工具。

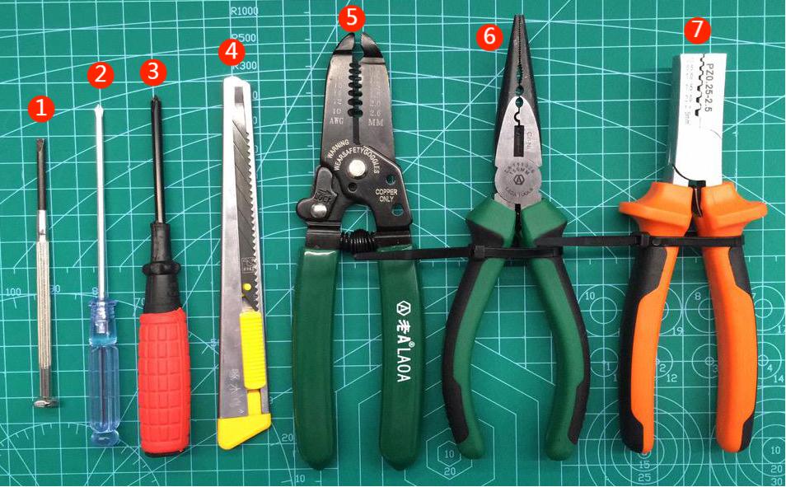
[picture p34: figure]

1 | 中号一字改锥
2 | 小号十字改锥
3 | 中号十字改锥
4 | 美工刀
5 | 剥线钳
6 | 尖嘴钳
7 | PZ 压线钳
2. 需要用到的材料。
1 | 2 芯 1 平方保护套软电线 0.2m
2 | 电源接头 DC 母头
3 | 预绝缘管型端子【1 平方管长 8mm】x4
3. 剥掉 2 芯电线两端保护套。

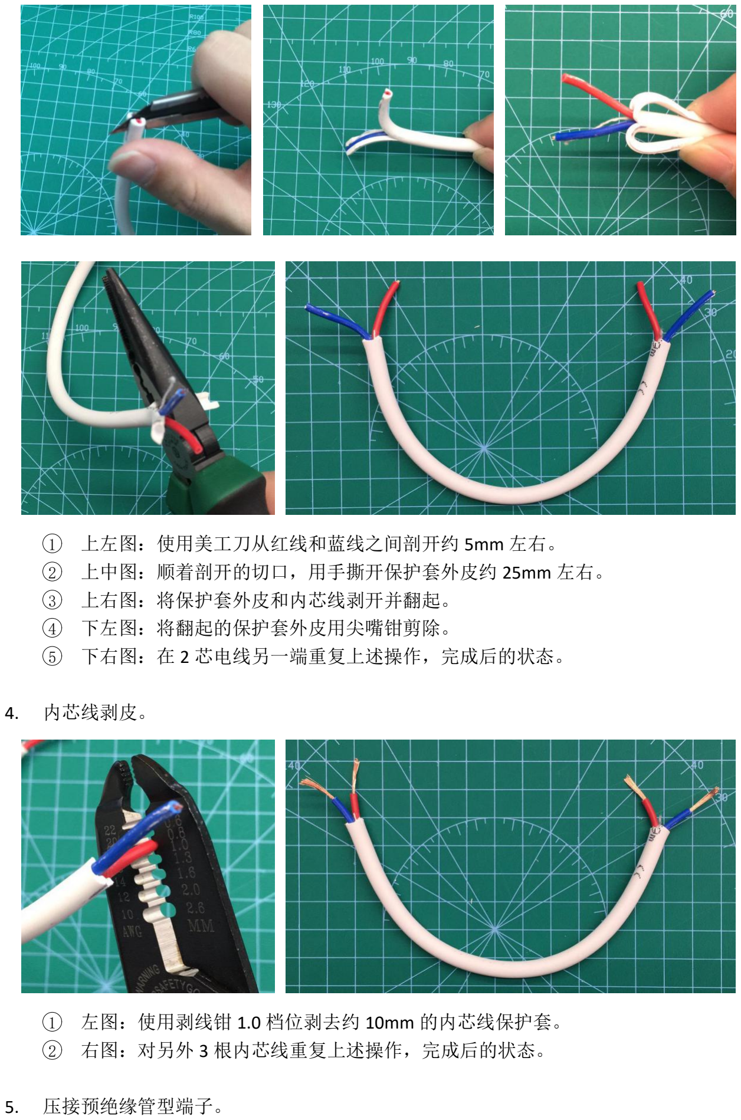
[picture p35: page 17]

1 | 上左图：使用美工刀从红线和蓝线之间剖开约 5mm 左右。
2 | 上中图：顺着剖开的切口，用手撕开保护套外皮约 25mm 左右。
3 | 上右图：将保护套外皮和内芯线剥开并翻起。
4 | 下左图：将翻起的保护套外皮用尖嘴钳剪除。
5 | 下右图：在 2 芯电线另一端重复上述操作，完成后的状态。
4. 内芯线剥皮。
1 | 左图：使用剥线钳 1.0 档位剥去约 10mm 的内芯线保护套。
2 | 右图：对另外 3 根内芯线重复上述操作，完成后的状态。
5. 压接预绝缘管型端子。

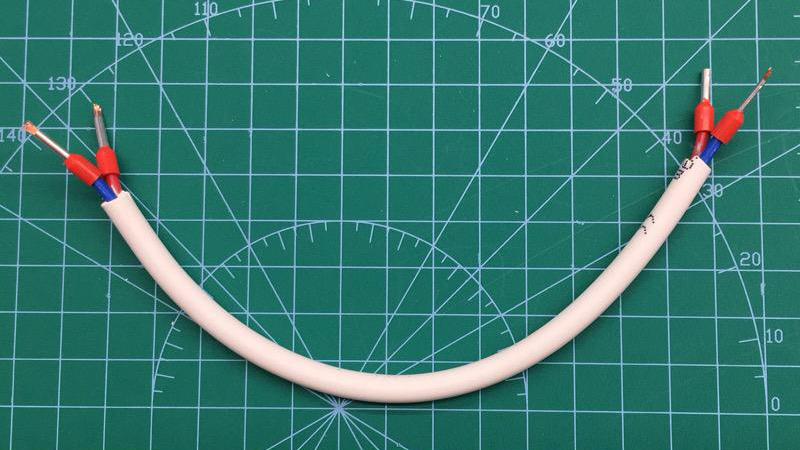
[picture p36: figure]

1 | 上左图：套上预绝缘管型端子。
2 | 上右图：使用 PZ 压线钳 1.0 档位，用力压接管型端子和线芯。
3 | 下图：对另外 3 根内芯线重复上述操作，完成后的状态。
4 | 注意：压接后露出的多余线芯，可以使用尖嘴钳截去。
6. 对接 CNC Shield V3 和 DC 母头

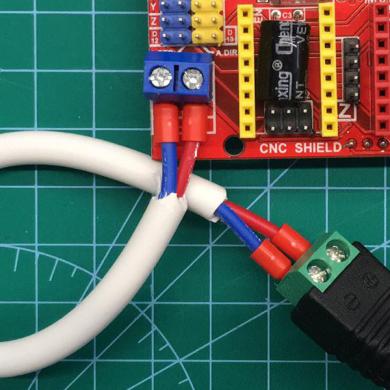
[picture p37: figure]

1 | 左图：将压接好的线头一端插入 DC 母头的接线槽中，并用中号十字改锥拧紧。
2 | 中图：将压接好的线头另一端插入 CNC Shield V3 的接线槽中，并用中号一字改锥
拧紧。
3 | 右图：CNC Shield V3 电源接口制作完成。
4 | 注意：接线时正负极不要接错。

## 3 软件部分

## 3.1 Arduino IDE

官网下载

1. 打开 Arduino 官网：https://www.arduino.cc/。
2. 鼠标移动到导航栏菜单 SOFTWARE 上，点击下拉菜单 DOWNLOADS 打开下载网页：
https://www.arduino.cc/en/software/。
3. 在 DOWNLOAD OPTIONS 下根据自己的操作系统选择适合自己的版本进行下载。
4. 若您使用 Windows 操作系统，建议下载 Windows ZIP file 版本，并在解压后的文件夹根 目录下新建一个文件夹 portable。 网盘下载

由于 Arduino 官网是境外网站，访问可能受限，我在百度网盘上镜像了一份最新（截至本文 档写作日期）的 Windows ZIP file 版本，地址及提取码如下：
1 | arduino-1.8.13-windows.zip https://pan.baidu.com/s/1vTS0KWl8ofQgZ1sEcmsdrA 提取码:m58s
2 | arduino-1.8.13-windows.exe https://pan.baidu.com/s/1ZwsYJ5x-x0vNcNG9frReAw 提取码：buqo

USB 转串口驱动官网下载

1. 若您采购了 Arduino Uno 官方版开发板，则串口驱动位于 Arduino IDE 的根目录下的
drivers 目录中。
2. 若您采购了副(ke)厂(long)的 Uno 开发板，则一般采用的是 CH340 USB 转串口芯片。
3. 在 bing 中搜索 ch340，搜索结果中的第一条：USB 转串口芯片:CH340 - 南京沁恒微电子 (http://www.wch.cn/product/CH340.html) 股份有限公司页面中，有各操作系统的驱动程序下载，如 CH341SER.EXE。

USB 转串口驱动网盘下载

1 CH341SER.EXE https://pan.baidu.com/s/1w1-0J5isymuUxMPFYX7-RQ 提取码:2cgj

## 3.2 Grbl firmware (Servo)

项目主页

1. Grbl：https://github.com/grbl/grbl v0.9j 及之前的版本。
2. Grbl Servo：https://github.com/robottini/grbl-servo 基于 v0.9i 支持伺服马达的版本。
3. config.h (T 站上的 DrawBot V1.1 项目)：https://www.thingiverse.com/download:3853123。 整合分支

我基于上述三部分整合了一个分支：https://github.com/zzhouj/grbl/tree/v0.9i_servo。您可以 在此分支中看到 Grbl Servo 对 Grbl v0.9i 所作的修改，以及 config.h (T 站上的 DrawBot V1.1
项目)进行了那些修改。 网盘下载

由于 Github 是境外网站，访问可能受限，我在百度网盘上镜像了一份最新（截至本文档写 作日期）的整合分支版本，地址及提取码如下：
1 grbl-0.9i_servo.zip https://pan.baidu.com/s/1hzgLwkzNqOI_1vCKqHr1qw 提取码:nj75

## 使用 Arduino IDE 编译上传 Grbl firmware (Servo)

推荐参考《Compiling Grbl》来了解如何使用 (https://github.com/grbl/grbl/wiki/Compiling-Grbl) Arduino IDE 编译上传 Grbl firmware。我这里也
写一份简要的操作指南：
1. 下载 arduino-1.8.13-windows.zip 到本地文件夹（如）E:\drawbot。解压到当前文件夹， 进入解压后生成的文件夹 E:\drawbot\arduino-1.8.13 新建一个文件夹 portable。
2. 下载 grbl-0.9i_servo.zip 到本地文件夹 E:\drawbot。解压到当前文件夹，解压后生成的文 件夹为 E:\drawbot\grbl-0.9i_servo。
3. 启动 Arduino IDE，可执行文件位于 E:\drawbot\arduino-1.8.13\arduino.exe。
4. 在 Arduino IDE 的菜单栏中选择【项目】【加载库】【添加.ZIP 库...】（也可添加文件夹），

选 择 文 件 夹 E:\drawbot\grbl-0.9i_servo\grbl 点 击 【 打 开 】 。 注 意 ： 并 不 是 打 开
grbl-0.9i_servo.zip 解压后的根目录，而是其子目录 grbl，其中包含源码和示例。
5. 在 Arduino IDE 的菜单栏中选择【文件】【示例】最后的三方库示例【grbl】【grblUpload】，
Arduino IDE 会在新的窗口中打开 grblUpload 示例的源码。注意：若未找到 grblUpload
示例，则说明添加库的路径搞错了，此时可以先将错误的库删除，然后重复上述步骤重
新加载正确的库。已安装的库文件夹位于：portable\sketchbook\libraries。
6. 使用 USB 连接 Arduino Uno 开发板，在 Arduino IDE 的菜单栏中选择【工具】【开发板】
选中 Arduino Uno。在 Arduino IDE 的菜单栏中选择【工具】【端口】选择您的开发板在 您的操作系统中的串口编号。
7. 点击 Arduino IDE 的菜单栏中【项目】【上传 Ctrl+U】，或者点击 Arduino IDE 的工具栏
中的第二个按钮（图标为向右的箭头）进行编译上传。

## 3.3 Inkscape

官网下载

1. 打开 Inkscape 官网：https://inkscape.org/。
2. 鼠标移动到导航栏菜单 DOWNLOAD 上，点击下拉菜单 Current Version 打开下载网页：
https://inkscape.org/release/inkscape-1.0.2/。
3. 根据自己的操作系统选择适合自己的版本进行下载。 网盘下载
1 | inkscape-1.0.2_2021-01-15_e86c870-x64.7z https://pan.baidu.com/s/1_9AQ3hUZ4wkzyRJYnAxCRQ 提取码：dd30
2 | inkscape-1.0.2_2021-01-15_e86c870879-x64.msi https://pan.baidu.com/s/1jfSZciDvzFo-w6nklTLJzA 提取码：kkf5

## 3.4 Axidraw Software

Axidraw 作为一个优秀的商业写字机器人，也提供了优秀的软件用户体验。

参考项目（T 站上的 DrawBot V1.1）使用了一个缺乏维护的（不支持最新版本的 Inkscape）
MI Inkscape Extension.zip (http://www.mediafire.com/file/ae0wquqornzc3o2/MI+Inkscape+Extension.zip) 插件（修改自 J Tech Photonics Laser Tool），此插件仅能够从 (https://github.com/JTechPhotonics/J-Tech-Photonics-Laser-Tool) Inkscape

的 SVG 文档中的路径（path）对象生成 G-Codes 文件。然后再将生成的 G-Codes 文件使用
Universal Gcode Sender (https://winder.github.io/ugs_website/) 发送给写字机器人（Grbl 固件）执行绘制操作。

Axidraw Software 作为 Inkscape 插件，提供了一站式用户体验。可以在 Inkscape 中将 SVG 文
档中的路径（path）对象，基本图形对象（矩形，圆形，椭圆，多边形等）生成 EBB 固件指 令，并实时发送到 Axidraw（EBB 固件）执行绘制操作（文本对象需要手工转换成路径对象， 或使用 Hershey Text 转换成笔刷字体）。最棒的是，可以在最新版的 Inkscape v1.0.2 中使用
最新版的 Axidraw Software v2.7.0（截至 2021 年 2 月 20 日）。

Axidraw Software 还提供了一些实用工具，如 Hatch fill（图案填充工具），Hershey Text（笔 刷字体替换工具），Plot Optimization（绘图顺序优化工具）等。建议阅读《AxiDraw User Guide》
来了解如何使用这些实用工具。 官网下载
1. Axidraw Software Installation（安装指南）： https://wiki.evilmadscientist.com/Axidraw_Software_Installation
2. AxiDraw User Guide（用户指南）： https://wiki.evilmadscientist.com/AxiDraw_User_Guide

网盘下载

1 | ad-ink_270_r2.zip https://pan.baidu.com/s/1vfdEkPS7AT7txzSeKlb1XA 提取码：noz4
2 | AxiDraw_Guide_v45.pdf https://pan.baidu.com/s/1RN7qX7OoyD-jPLgXlQR-pA 提取码：sady

## 3.5 Generate G-Codes patch for AxiDraw Extensions for Inkscape

我在 AxiDraw Extensions for Inkscape v2.7.0 的基础上写了一个补丁，可以利用 AxiDraw Extensions 的预览模式生成适合 Grbl 固件使用的 G-Codes 代码。

1 | Enable offline preview mode; Simulate plotting only：Axidraw 离线预览模式开关。
2 | Preview mode rendering：选择预览模式时需要渲染的轨迹，包括：无，抬笔路径，
绘制路径，全部路径。
3 | Generate G-Codes：生成 G-Codes 的开关。
4 | G-Code for linear motion：直线移动命令，默认值为：G1。
5 | G-Code for pen raise：抬笔命令，默认值为：M5。
6 | G-Code for pen lower：放笔命令，默认值为：M3 S30（S 参数为伺服电机转动的角
度值）。
7 Delay (seconds) for pen raise or lower：抬笔放笔命令执行之后等待的时间（单位：
秒），默认值为：0.2 秒。
8 Feedrate (mm/min) for pen raise：抬笔时的直线运动速度（单位：毫米每分钟），
默认值为：3000 毫米每分钟。
9 Feedrate (mm/min) for pen lower：绘制（放笔）时的直线运动速度（单位：毫米每
分钟），默认值为：500 毫米每分钟。
10 注意在选项标签页点击应用按钮不会有任何效果，要生成 G-Codes 需要在绘制标签 页下点击应用按钮。

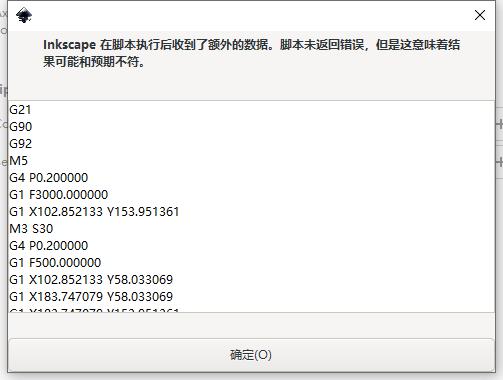
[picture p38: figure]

1 图为生成的 G-Codes 代码。 安装步骤

1. 下载并解压 ad-ink_270_r2.zip。
2. 下载并解压 ad-ink_270_r2_gen_gcodes_v0.1.zip。
3. 复制并覆盖 ad-ink_270_r2_gen_gcodes_v0.1 文件夹下的文件到 ad-ink_270_r2 文件夹。
4. 复制并覆盖 ad-ink_270_r2 文件夹下的文件到 Inkscape 插件安装目录。 官网下载
1. https://github.com/zzhouj/axidraw/releases/tag/ad-ink_270_r2_gen_gcodes_v0.1

网盘下载

1 ad-ink_270_r2_gen_gcodes_v0.1.zip https://pan.baidu.com/s/1zl0b4YAfTjleaBficXRGSA 提取码：uqp2

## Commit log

2021-01-31 3mm铝合金板材定制加工
    [XY轴联合支架.DXF, Y轴尾端.DXF, Y轴首端.DXF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]
2021-01-31 写字机器人（总装）
    [2040铝合金型材盖板.SLDPRT, 2040铝合金型材盖板（已紧固——T型螺母）.SLDASM, 2040铝合金型材盖板（已紧固）.SLDASM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]
2021-01-31 各部分材料清单
    [42步进电机（减震垫同步轮）.xls, XY轴联合支架（轴承滑轮）.xls, X轴.xls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]
2021-01-31 添加电子部分材料清单，并添加价格
    [BOM.xls]
2021-02-01 CNC Shield电源适配器及电源接头
    [BOM.xls]
2021-02-06 装配及用户手册~未完待续
